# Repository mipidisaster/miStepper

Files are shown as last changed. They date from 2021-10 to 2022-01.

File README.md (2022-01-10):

# miStepper
This library contains the files and support for creating and installed code for the miStepper Device.e with this device).

# Linked libraries:
## milibrary
This library makes use of an extra repository - ['milibrary'](https://github.com/mipidisaster/miLibrary), which is not included within this repository; due to it being a seperate one. So this will need to be included...
> It doesn't matter were this is stored, however it should be at a high enough level that any lower level scripts can make reference to it.

```
<project root>
  ├─ milibrary
  │      └─ <contents>
  └─ < other folders >
```

# Stack overview
> To be added

# Build Tree
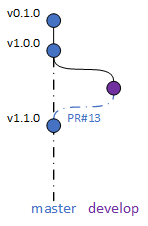
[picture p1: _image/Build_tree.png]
build tree


v1.1.0
* Changes made to the software to incorporate the motor HAL - Fan/Stepper, as well as changes to the USART interface (making it common with the 'miStepper_ROS' repository
* Issues [#4](https://github.com/mipidisaster/miStepper/issues/4) and [#5](https://github.com/mipidisaster/miStepper/issues/5) fixed
* Issue [#7](https://github.com/mipidisaster/miStepper/issues/7), partial progress has been made on working this - mainly that a single task now exists for the motors
* Submodules introduced for the 'miStepper_ROS' and 'miLibrary' repositories so as to manage which version(s) are appliable to this

v1.0.0
* Major update of build, changing the electronics (PCB):
  1. PCB/Electronics updated to include new Stepper IC - (issue [#1](https://github.com/mipidisaster/miStepper/issues/1))
  2. Hardware filtering on the voltage/current monitors
  3. Extra temperature sensors added - 2 onboard sensors, and 2 external sensors
  4. CAN interface improved, such that it not is compliant to the protocol/hardware
  5. 4 layer PCB, to aid thermal cooling

* Software code updated:
  1. Supports latest release of 'milibrary' - [v0.2.1](https://github.com/mipidisaster/miLibrary/tree/v0.2.1)
     * Closing issue [#3](https://github.com/mipidisaster/miStepper/issues/3)
  2. Update to support latest hardware additions
  > Note, external sensor support not provided currently, to be added in next release
  
  3. Re-structing of the code, such that it follows the ['Layered Software Architecure'](https://github.com/mipidisaster/miLibrary/wiki/Software-Architecture) as per milibrary wiki - (issue [#2](https://github.com/mipidisaster/miStepper/issues/2))

v0.1.0
* Initial release (to be used with [milibrary v0.1.0](https://github.com/mipidisaster/miLibrary/tree/v0.1.0))

# Wiki
The wiki for this can be found within the Github repository for this - > to be added

See https://github.com/mipidisaster/miLibrary/wiki for basic information on Eclipse setup/remote ROS downloading...

# Issues
If you find any issues with this library, please capture them within the Github repository issue area - https://github.com/mipidisaster/miStepper/issues.

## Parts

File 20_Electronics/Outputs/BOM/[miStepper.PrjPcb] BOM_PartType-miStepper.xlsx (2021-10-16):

Comment | Description | Designator | Footprint | LibRef | Value | Quantity | Layer
Res | Resistor | R10, R11, R12, R13 | RESC2012X06N (0805) | Res | 680mOhm/0.5W | 4 | Top
600R @ 100MHz | Inductor with ferrite bead | L1 | INDC1608X06N | Ferrite Bead | 600R @ 100MHz | 1 | Bottom
Cap Semi | Capacitor (Semiconductor SIM Model) | C14 | CAPC3216X06N (1206) | Cap Semi | 330nF/50V | 1 | Bottom
Cap Semi | Capacitor (Semiconductor SIM Model) | C12, C15, C18, C23_A, C23_C, C24_A, C24_C | CAPC1608X06N (0603) | Cap Semi | 100nF +/-5% | 7 | Bottom, Bottom, Top, Bottom, Bottom, Bottom, Bottom
Cap Semi | Capacitor (Semiconductor SIM Model) | C2, C3, C4, C5, C9, C20, C22, C25 | CAPC1608X06N (0603) | Cap Semi | 100nF | 8 | Top, Top, Bottom, Bottom, Bottom, Bottom, Top, Bottom
Res | Resistor | R14, R15 | RESC1608X06N (0603) | Res | 47k | 2 | Bottom
Res | Resistor | R8 | RESC1608X06N (0603) | Res | 39k | 1 | Bottom
Cap Pol | Polarized Capacitor (Surface Mount) | C13 | CAPAE7066X77M | Cap Pol | 33uF/50V | 1 | Top
Res | Resistor | R16 | RESC1608X06N (0603) | Res | 22k | 1 | Bottom
Res | Resistor | R9 | RESC1608X06N (0603) | Res | 18k | 1 | Top
Cap Semi | Capacitor (Semiconductor SIM Model) | C19, C21 | CAPC1608X06N (0603) | Cap Semi | 10uF | 2 | Bottom, Top
Cap Semi | Capacitor (Semiconductor SIM Model) | C7, C16 | CAPC1608X06N (0603) | Cap Semi | 10nF | 2 | Bottom
Res | Resistor | R1, R19, R20 | RESC1608X06N (0603) | Res | 10K | 3 | Top, Bottom, Bottom
Res | Resistor | R3, R5, R17, R21_A, R21_C | RESC1608X06N (0603) | Res | 9.76k +/-1% | 5 | Bottom, Bottom, Top, Bottom, Bottom
Res | Resistor | R2 | RESC1608X06N (0603) | Res | 7.5k | 1 | Top
Res | Resistor | R4 | RESC1608X06N (0603) | Res | 6.49k +/-1% | 1 | Bottom
Cap Semi | Capacitor (Semiconductor SIM Model) | C1 | CAPC1608X06N (0603) | Cap Semi | 4.7uF | 1 | Bottom
Res | Resistor | R18 | RESC1608X06N (0603) | Res | 4.32k +/-1% | 1 | Top
Res | Resistor | R6 | RESC1608X06N (0603) | Res | 1.96k +/-1% | 1 | Bottom
Cap Semi | Capacitor (Semiconductor SIM Model) | C6, C8 | CAPC1608X06N (0603) | Cap Semi | 1uF | 2 | Bottom
Cap Semi | Capacitor (Semiconductor SIM Model) | C11, C17 | CAPC1608X06N (0603) | Cap Semi | 1nF | 2 | Top
Res | Resistor | R7 | RESC1608X06N (0603) | Res | 1k | 1 | Bottom
Cap Semi | Capacitor (Semiconductor SIM Model) | C10 | CAPC1608X06N (0603) | Cap Semi | 0.1uF | 1 | Bottom
Res | Resistor | RS1_A, RS1_C | RESC2012X06N (0805) | Res | 0.05+/-1% | 2 | Bottom
AD7415ARTZ-1500RL7 | I2C Temperature Sensor | U4, U7 | SOT95P280X145-5N | AD7415ARTZ-1500RL7 |  | 2 | Bottom, Top
AS5047D |  | U9 | TSSOP14 | AS5047D |  | 1 | Bottom
CS30xL | High side current sense high voltage op amp | U8_A, U8_C | SOT95P280X145-5N | CS30xL |  | 2 | Bottom
GY-BME280 BREAKOUT |  | U5, U6 | GY-BME280 BREAKOUT | GY-BME280 BREAKOUT |  | 2 | None
JST PH Series, 2mm Pitch 6 Way 1 Row Right Angle PCB Header, Solder Termination, 2A Source: Datasheet | Custom header for miStepper | JP2 | S6B-PH-SM4-TB(LF)(SN) | miStepper-Connector |  | 1 | None
MC33873 | Motor | JP4 | JP1Y | MC33873 |  | 1 | Top
NEMA17 | Stepper Motor | JP3 | S4B-PH-SM4-TB(LF)(SN) | NEMA17 |  | 1 | Top
NMOS-2 | N-Channel Power MOSFET | Q1 | SOT230P700X180-4N | NMOS-2 |  | 1 | Top
Option_Res | Resistor | SB1 | RESC1608X06N (0603) | Option_Resistor |  | 1 | Top
Schottky Diode | Schottky Rectifier | D1 | SODFL350X115-2N | Diode |  | 1 | Bottom
SN65HVD233 | 3.3V CAN Bus Transceiver | U2 | SOIC127P600X175-8N | SN65HVD23x |  | 1 | Top
ST-LINK_USART | Header, 8-Pin | JP1 | MHDR1X8 | MHDR1X8 |  | 1 | Top
STM32L431CC | STM32 ARM-based 32-bit MCU with 32 Kbytes Flash, 48-pin LQFP, Industrial Temperature | U1 | LQFP48_L | STM32L431CC |  | 1 | Top
STSPIN820 | Stepper IC | U3 | QFN50P400X400X110-25N | STSPIN820 |  | 1 | Top

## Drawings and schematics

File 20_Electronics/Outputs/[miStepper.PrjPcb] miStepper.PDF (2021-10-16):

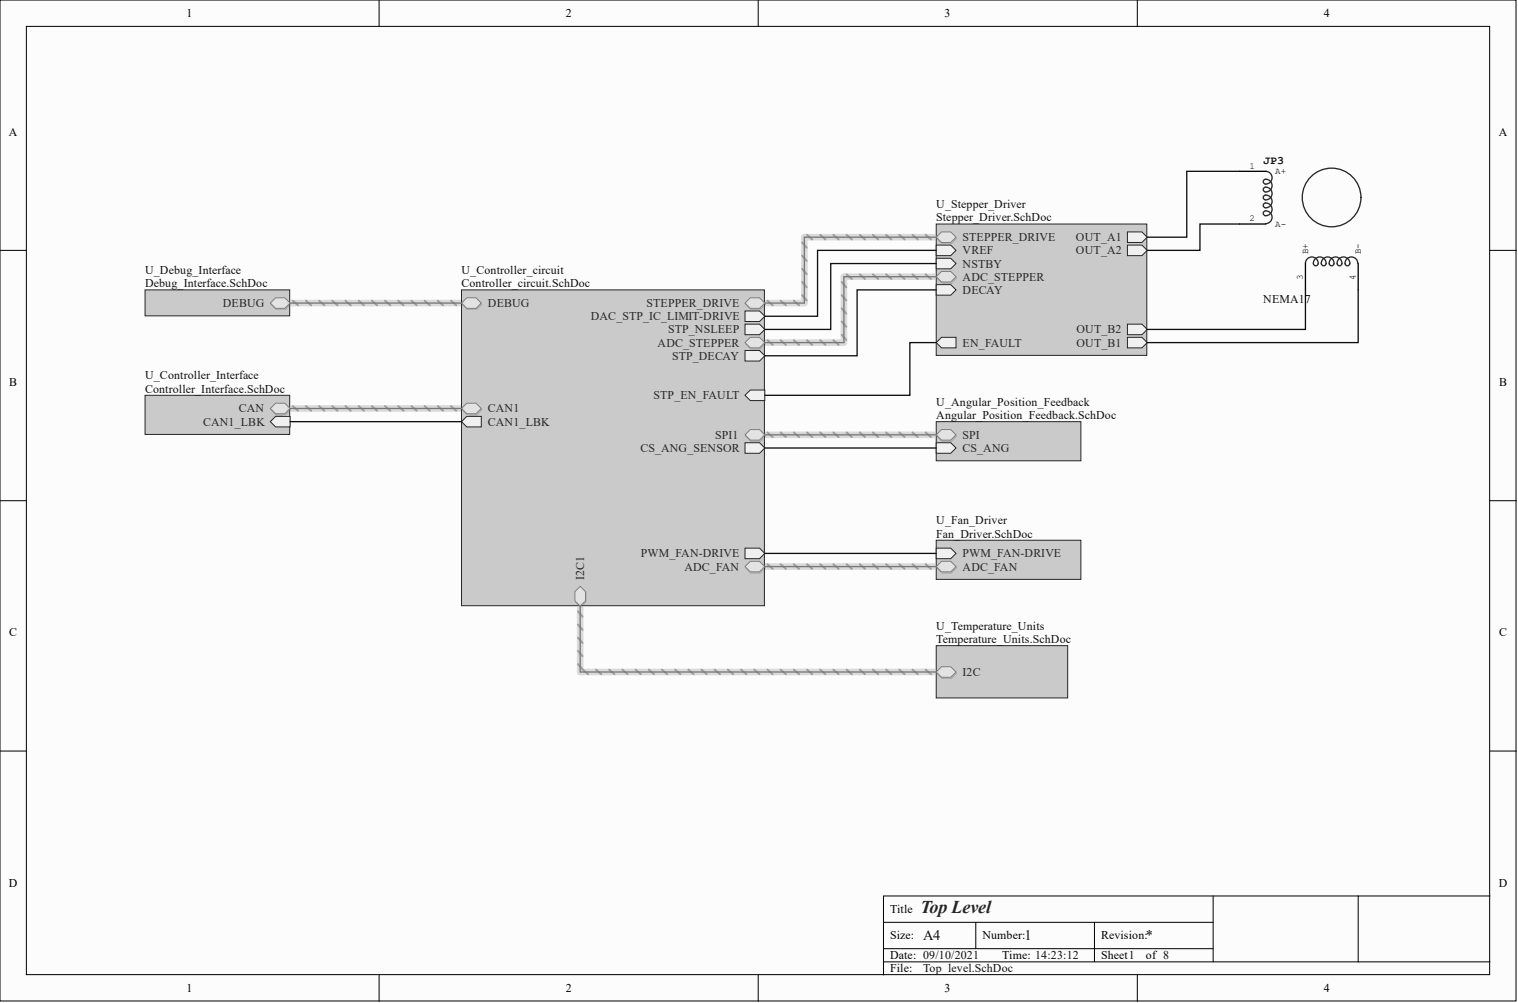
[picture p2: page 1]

Title Top Level

Size: A4 | Number: 1 | Revision: *
Date: 09/10/2021 Time: 14:23:12 | | Sheet of

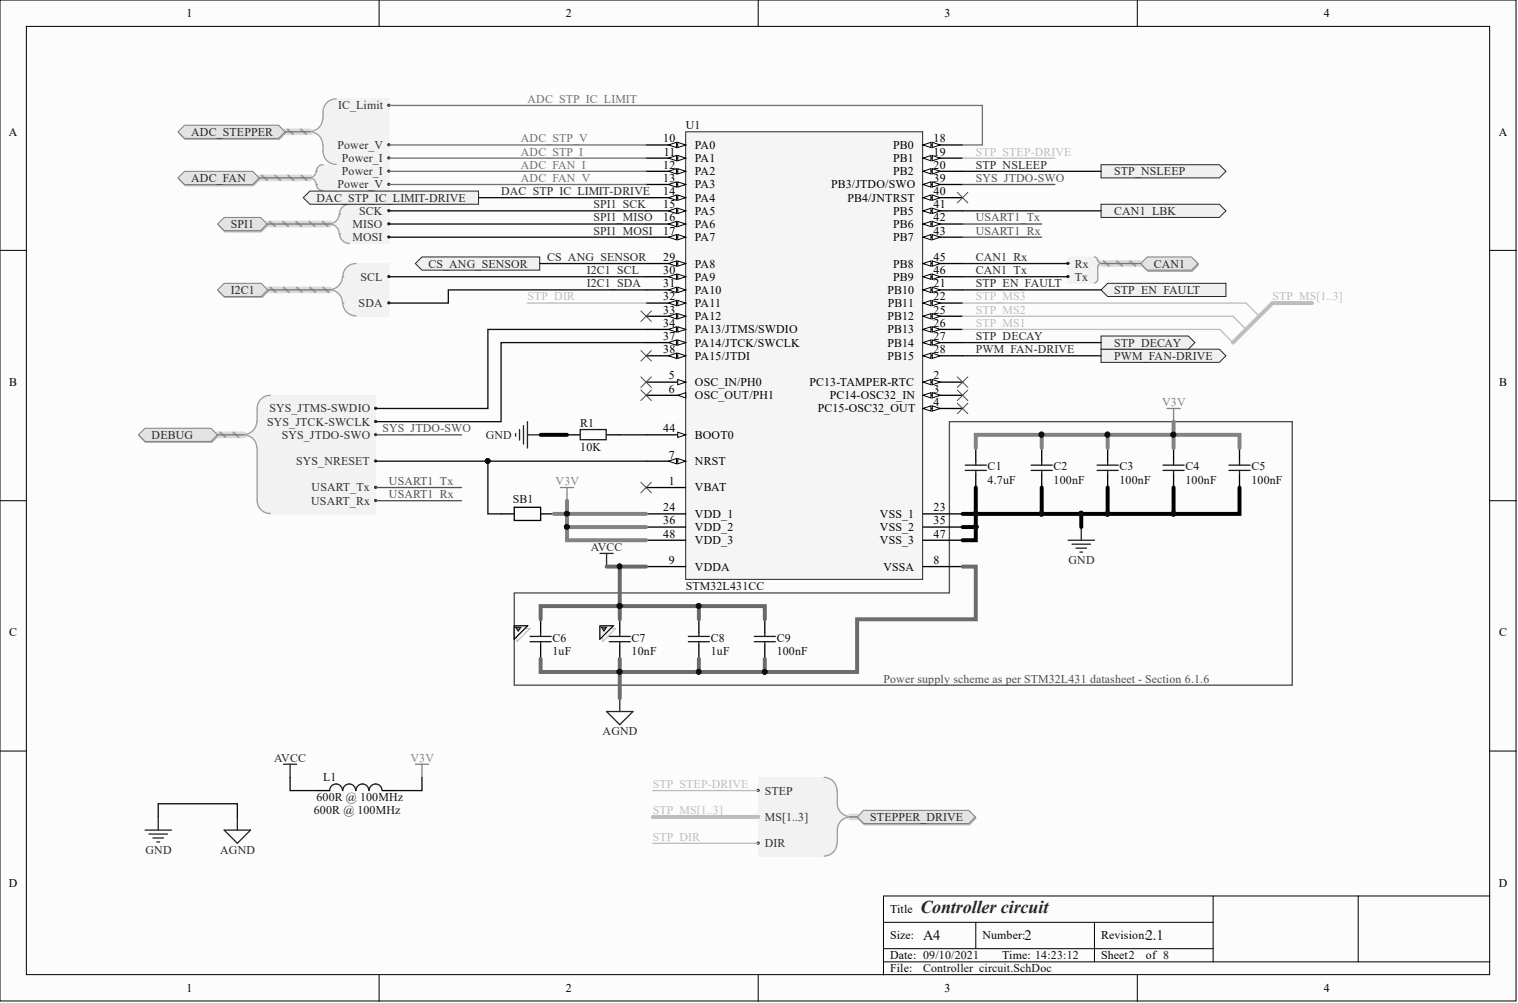
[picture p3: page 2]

Power supply scheme as per STM32L431 datasheet - Section 6.1.6

Title Controller circuit

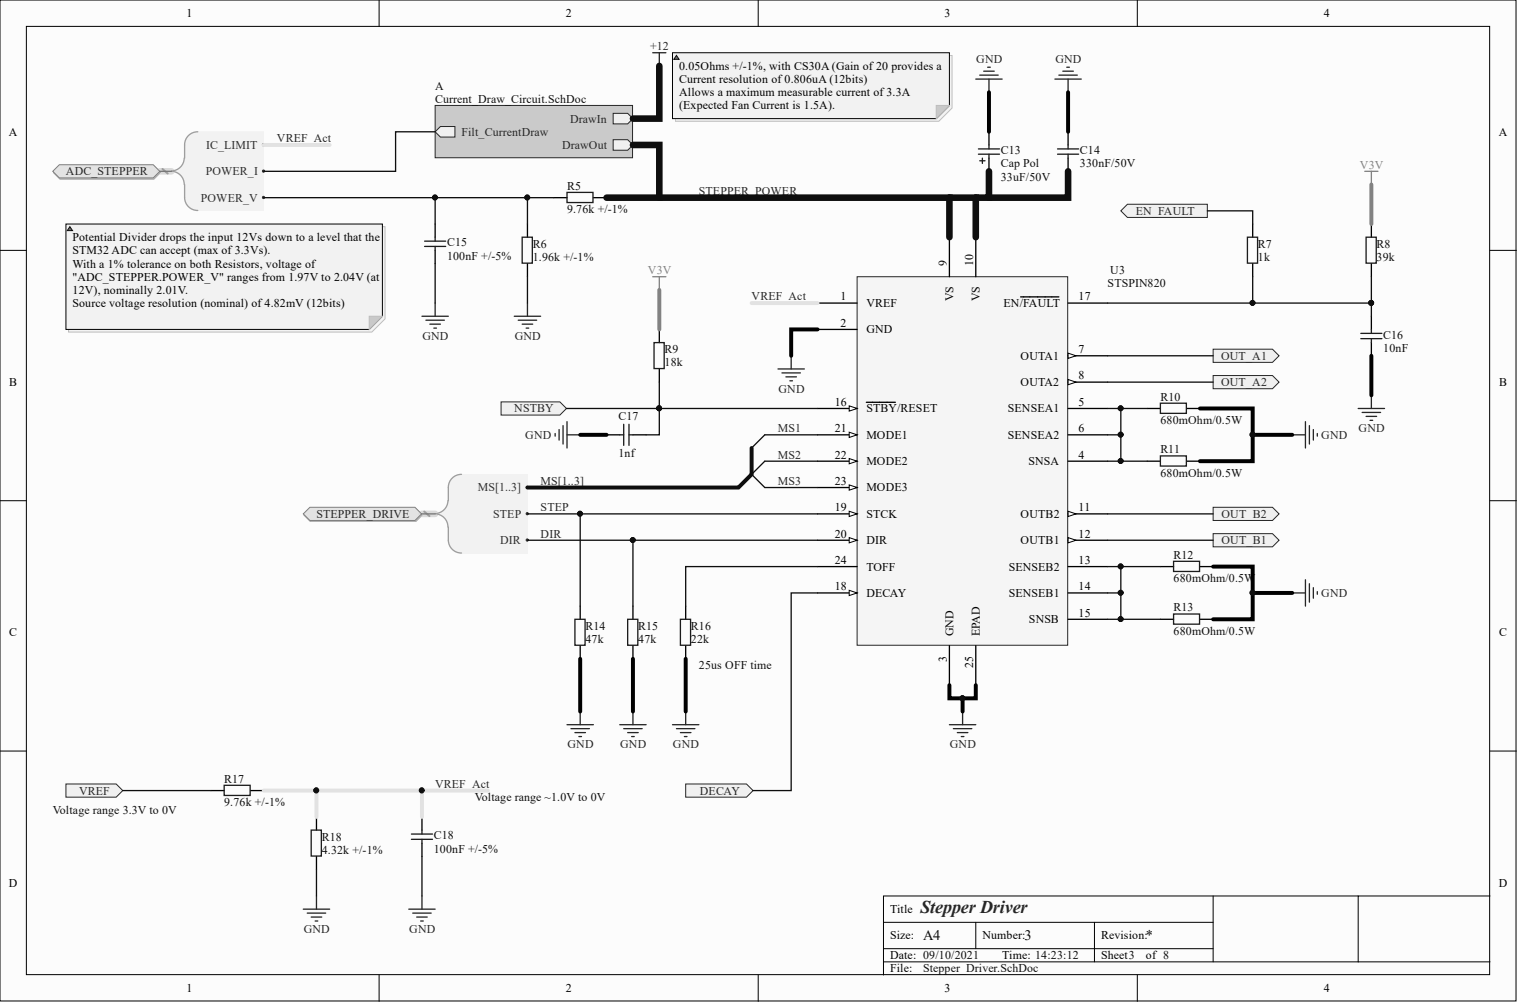
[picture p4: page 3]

0.05Ohms +/-1%, with CS30A (Gain of 20 provides a
Current resolution of 0.806uA (12bits)
Allows a maximum measurable current of 3.3A
(Expected Fan Current is 1.5A).

Potential Divider drops the input 12Vs down to a level that the
STM32 ADC can accept (max of 3.3Vs).
With a 1% tolerance on both Resistors, voltage of
"ADC_STEPPER.POWER_V" ranges from 1.97V to 2.04V (at
12V), nominally 2.01V.
Source voltage resolution (nominal) of 4.82mV (12bits)

GND 2

MODE1 21 MODE2 22 MODE3 23 STCK 19 | 680mOhm/0.5W R11

TOFF 24
DECAY 18 | 680mOhm/0.5W

Title Stepper Driver

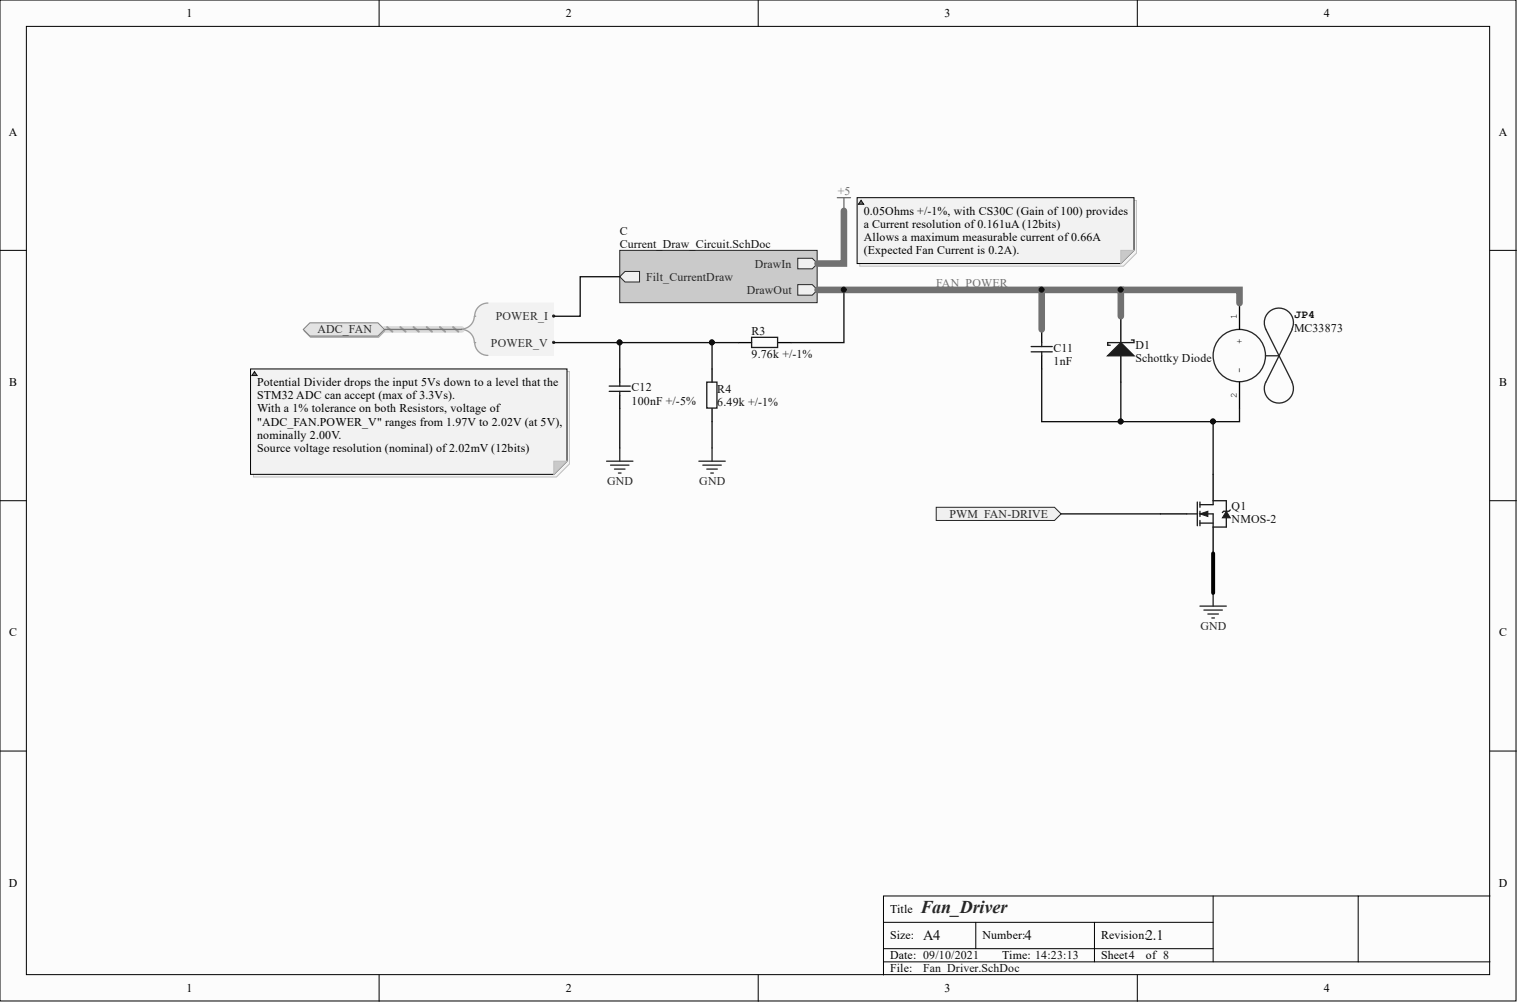
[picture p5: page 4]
DrawIn DrawOut; ial D; o a level t; hat t; t (max of 3.3; lerance o; h Res; ors, v; tage of; V" ran; ges from 1.9; urce v; tage res; nal) of 2.0; hms +/-1; 0C (Gai; 0) pro; a Curren; t res; s a max; imum meas; le curren; pected Fan Curren

der dro
DC can accep

T i t l e Fan_ Driver

Size: A | N umber: | Rev i s n 2.1

/ T ime: : | | Sheet f

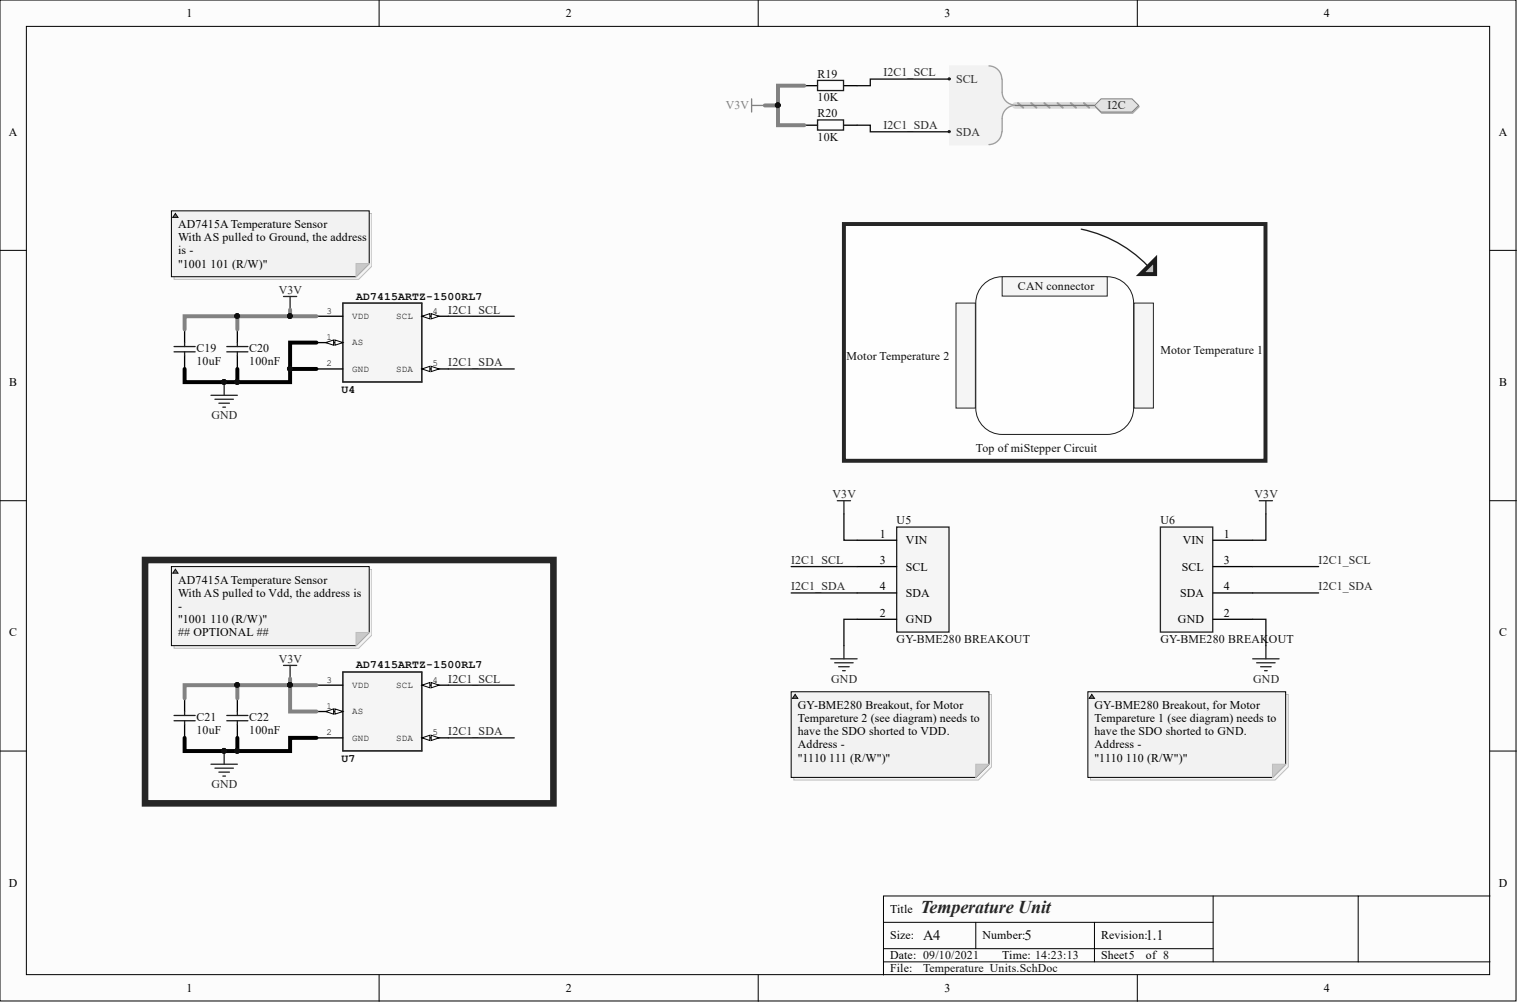
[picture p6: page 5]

AD7415A Temperature Sensor
With AS pulled to Ground, the address

Top of miStepper Circuit

With AS pulled to Vdd, the address is
## OPTIONAL ##

GY-BME280 Breakout, for Motor
Tempareture 2 (see diagram) needs to
have the SDO shorted to VDD.
Address -

Tempareture 1 (see diagram) needs to
have the SDO shorted to GND.

Title Temperature Unit

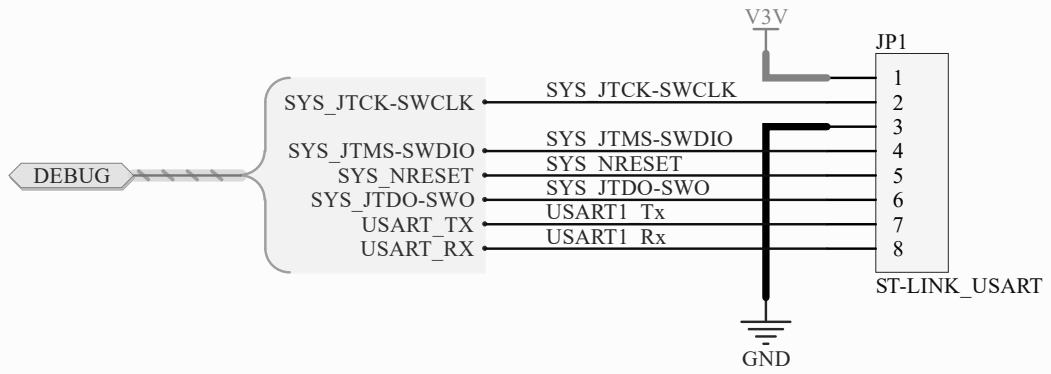
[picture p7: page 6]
Debug Interface6; PIJP102 NLSYS0JTCK0SWCLK; PODEBUG; PIJP106 NLSYS0JTDO0SWO; PIJP104 NLSYS0JTMS0SWDIO PIJP105 NLSYS0NRESET; PIJP108 NLUSART10Rx; PIJP107 NLUSART10Tx; PODEBUG0SYS0JTCK0SWCLK PODEBUG0SYS0JTDO0SWO PODEBUG0SYS0JTMS0SWDIO PODEBUG0SYS0NRESET PODEBUG0USART0RX PODEBUG0USART0TX

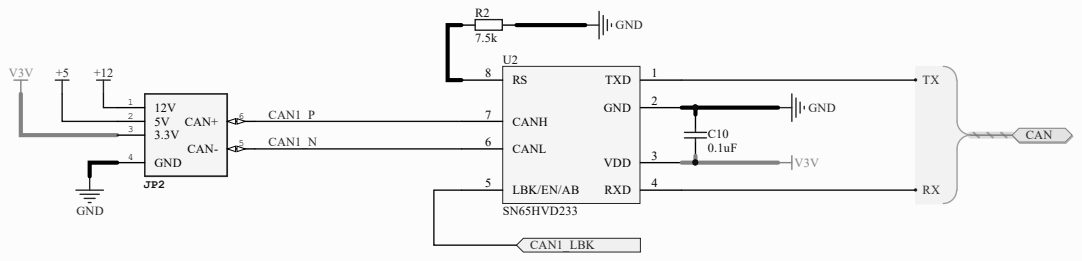
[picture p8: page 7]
RXD; 4 LBK/EN/AB 5; CANL 6; CANH 7; GND 4

Title Board Interfaces

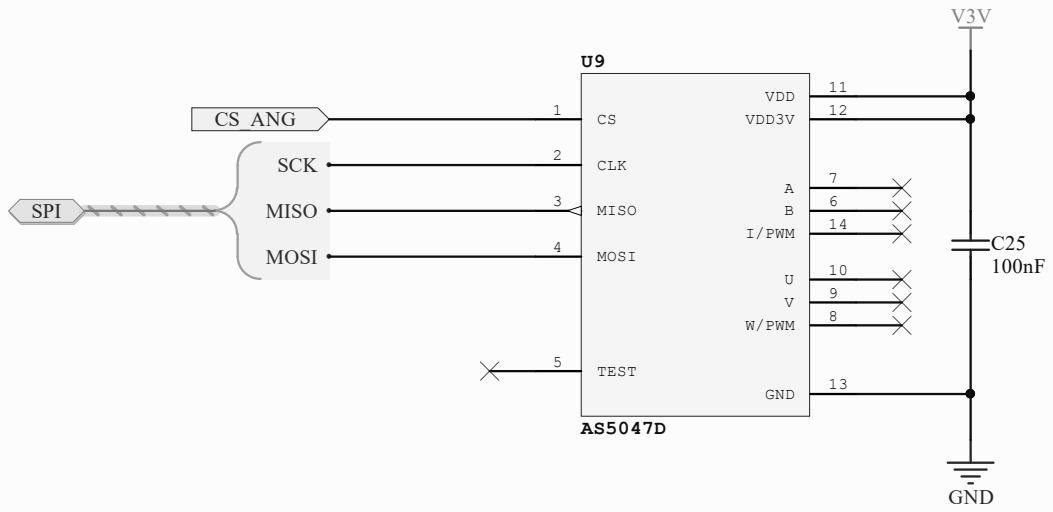
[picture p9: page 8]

T i t l e Angular Position Feedb ack

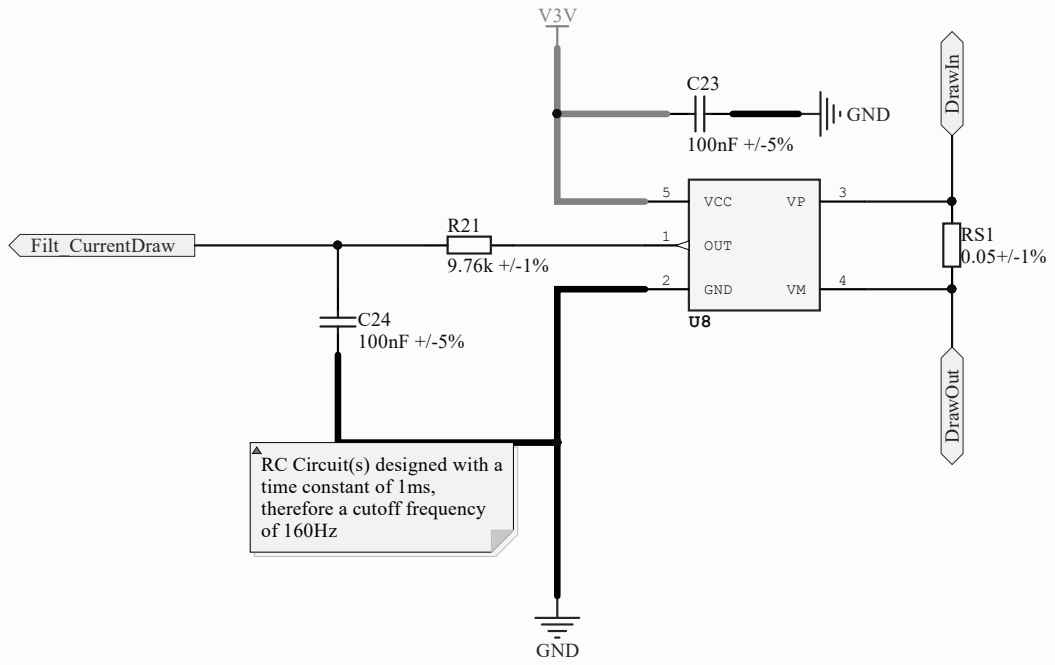
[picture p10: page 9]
DrawIn DrawOut; RC Circu; t(s) des; ned w; ime co; t of 1ms, herefore a cu; off freq

T i t l e Current Draw Senso r

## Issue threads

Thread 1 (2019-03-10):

Change Stepper IC

mipidisaster, 2019-03-10:
See about updating the Stepper IC to an STMicroelectronics component: STSPIN820
As gives better stepping control - 1/256 of a step!!

mipidisaster, 2019-03-10:
Check the schematic and gerbers of the dev board - IHM14A1

mipidisaster, 2021-10-16:
At v1.0.0 (585d8fb) STSPIN820 has been added to the PCB

Closed 2021-10-16.

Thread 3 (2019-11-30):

Highest Microstep not selected

mipidisaster, 2019-11-30:
During test phase - StepperTest2 - it was noticed that the highest microstep resolution (1/16) couldn't be selected with the current software version.
Testing has continued, however issue needs to be resolved.

mipidisaster, 2019-11-30:
Expect that the issue could be due to the Stepper driver, #2 (Library project).
Additionally the calcPosition logic needs to be looked into in more detail...

mipidisaster, 2019-12-01:
Found the issue:
https://github.com/mipidisaster/miStepper/blob/09903c70077cd2d019771f57bcddb5c358ebf495/30_Software/Embed/tasks/outputs/stepper_hal/stepper_hal.h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

Maximum gear should be 0x07!

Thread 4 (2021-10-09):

Stepper HAL missing

mipidisaster, 2021-10-09:
With the latest build there are no HAL interfaces for the Stepper task. So unable to actually control the motor in any way.

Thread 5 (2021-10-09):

USART controller missing links to the FAN/STEPPER

mipidisaster, 2021-10-09:
Current USART task - built off devel - "miStepperUSART" is missing connections for the FAN and STEPPER controller

mipidisaster, 2022-01-10:
Issue closed with pull request #13

Closed 2022-01-10.

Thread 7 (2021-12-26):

Driver tasks

mipidisaster, 2021-12-26:
Might be worth removing the specific tasks for the stepper motor and fan motor control. As this could be simply a function which updates the parameters for the drivers, removing the need for seperate tasks which basically do nothing...

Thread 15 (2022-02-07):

BME280 introduction to miStepper device

mipidisaster, 2022-02-07:
With the new hardware standard for miStepper, there are 2 external temperature sensors to be used to get the temperature of the motor.
These sensors are BME280 connected via I2C. This needs to be added to the build

mipidisaster, 2022-03-05:
This is a MINOR version introduction - so version number should go up by 0.1.0 minimum.

mipidisaster, 2022-03-06:
This is a MINOR version introduction - so version number should go up by 0.1.0 minimum (miStepper).

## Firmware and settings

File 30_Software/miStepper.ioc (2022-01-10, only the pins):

Mcu.UserName=STM32L431CBTx
PA0.GPIO_Label=ADC_STP_V
PA0.Signal=ADCx_IN5
PA1.GPIO_Label=ADC_STP_I
PA1.Signal=ADCx_IN6
PA10.Signal=I2C1_SDA
PA11.GPIO_Label=STP_DIR
PA11.Signal=GPIO_Output
PA2.GPIO_Label=ADC_FAN_I
PA2.Signal=ADCx_IN7
PA3.GPIO_Label=ADC_FAN_V
PA3.Signal=ADCx_IN8
PA4.GPIO_Label=DAC_STP_IC_LIMIT-DRIVE
PA4.Signal=COMP_DAC11_group
PA5.Signal=SPI1_SCK
PA6.Signal=SPI1_MISO
PA7.Signal=SPI1_MOSI
PA8.GPIO_Label=CS_ANG_SENSOR
PA8.Signal=GPIO_Output
PA9.Signal=I2C1_SCL
PB0.GPIO_Label=ADC_STP_IC_LIMIT
PB0.Signal=ADCx_IN15
PB1.GPIO_Label=STP_STEP-DRIVE
PB1.Signal=TIM1_CH3N
PB11.GPIO_Label=STP_MS3
PB11.Signal=GPIO_Output
PB12.GPIO_Label=STP_MS2
PB12.Signal=GPIO_Output
PB13.GPIO_Label=STP_MS1
PB13.Signal=GPIO_Output
PB14.GPIO_Label=STP_DECAY
PB14.Signal=GPIO_Output
PB15.GPIO_Label=PWM_FAN-DRIVE
PB15.Signal=S_TIM15_CH2
PB2.GPIO_Label=STP_NSLEEP
PB2.Signal=GPIO_Output
PB6.Signal=USART1_TX
PB7.Signal=USART1_RX

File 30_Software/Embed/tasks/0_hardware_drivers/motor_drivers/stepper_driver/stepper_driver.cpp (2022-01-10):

/**************************************************************************************************
 * @file        stepper_driver.cpp
 * @author      Thomas
 * @brief       Source file for Stepper Motor task handler
 **************************************************************************************************
  @ attention

  << To be Introduced >>

 *************************************************************************************************/
#include "tasks/0_hardware_drivers/motor_drivers/stepper_driver/stepper_driver.hpp"
#include "tasks/0_hardware_drivers/motor_drivers/motor_driver.h"
// C System Header(s)
// ------------------
#include <stdint.h>

// C++ System Header(s)
// --------------------
// None

// Other Libraries
// ---------------
// None

// Project Libraries
// -----------------
#include "stm32l4xx_hal.h"              // Include the HAL library
#include "main.h"                       // Include main header file, as this contains the defines
                                        // for GPIO signals
#include "tim.h"                        // Include the timer header file, as this contains the
                                        // htim1 handle

#include "tasks/0_hardware_drivers/motor_drivers/stepper_driver/stepper_driver_parameters.hpp"

#include "tasks/1_hardware_arbitration_layer/istepper_hal.hpp"
#include "tasks/1_hardware_arbitration_layer/itimer_hal.hpp"

#include "FileIndex.h"
//~~~~~~~~~~~~~~~~~~~~
#include FilInd_GPIO___HD               // Include the GPIO class handler
#include FilInd_StpCOREHD               // Include the Stepper CORE class handler

#ifdef zz__StepperDMAControl__zz
#include FilInd_StpDMA_HD               // Include the Stepper DMA class handler

#else
#include FilInd_StpTIM_HD               // Include the Stepper TIM class handler

#endif
//=================================================================================================

extern DMA_HandleTypeDef hdma_tim1_ch3; // Declare a DMA handle used for the TIM1

namespace _motor::_stepper {
/**************************************************************************************************
 * Define any private variables
 * ~~~~~~~~~~~~~~~~~~~~~~~~~~~~
 *************************************************************************************************/
#ifdef zz__StepperDMAControl__zz
static StepperDMA   *lc_handle;         // Pointer to the StepperDMA class handle, for interrupt
                                        // use

#else
static StepperTIM   *lc_handle;         // Pointer to the StepperTIM class handle, for interrupt
                                        // use

#endif

/**************************************************************************************************
 * Define any private function prototypes
 * ~~~~~~~~~~~~~~~~~~~~~~~~~~~~~~~~~~~~~~
 *************************************************************************************************/
uint32_t determineCountRate(uint8_t microstep);

//=================================================================================================

/**
  * @brief:  Setup and initialise the Stepper Class
  * @param:  void const, not used
  * @retval: None (void output)
  */
void setup(void) {
    // Generate the GPIO pins outside of 'Stepper' handle scope
    // ========================================================
    static GPIO    STP_DIR(    STP_DIR_GPIO_Port,       STP_DIR_Pin,        GPIO::kOutput);
    static GPIO    STP_MS[3]={{STP_MS1_GPIO_Port,       STP_MS1_Pin,        GPIO::kOutput},
                              {STP_MS2_GPIO_Port,       STP_MS2_Pin,        GPIO::kOutput},
                              {STP_MS3_GPIO_Port,       STP_MS3_Pin,        GPIO::kOutput} };

    static GPIO    STP_DECAY(  STP_DECAY_GPIO_Port,     STP_DECAY_Pin,      GPIO::kOutput);
    static GPIO    STP_SLEEP(  STP_NSLEEP_GPIO_Port,    STP_NSLEEP_Pin,     GPIO::kOutput);


    // Disable the Stepper IC, by pulling ENABLE/SLEEP high, and RESET low:
    STP_SLEEP.setValue(GPIO::State::kLow);      // Set Sleep  pin to LOW  '0'   (Device Asleep)
    STP_DECAY.setValue(GPIO::State::kLow);      // Set Decay  pin to Low  '0'   (Mixed Decay mode)
    // Create Stepper(DMA) class
    // =========================
#ifdef zz__StepperDMAControl__zz
    static StepperDMA
#else
    static StepperTIM
#endif
            STSPIN820(&htim1, &hdma_tim1_ch3,
                // Generate the output signal for STEP 'pulse'
            ( TIM_CCxN_ENABLE << TIM_CHANNEL_3 ),   // The output channel pin for enabling the
                                                    // output for 'Capture/Compare 3'
            // Linked GPIO pins - Reset(Sleep), Direction and Microstep
            &STP_SLEEP, &STP_DIR, &STP_MS[0], 3,
            200 * 256,

   /* Setup the 'Stepper' handler so that
    *      [1] The linked DMA used to generate the STEP 'pulse', which is Capture/Compare 3
    *      [2] Provide the BIT position for enabling/disabling in 'DIER' register for TIM linkage
    *          to DMA
    *      [3] Provide the BIT position within TIM 'EGR' to generate a 'Capture/Compare 3' event
    *      [4] Provide the BIT position within TIM 'SR' to check for a 'Capture/Compare 3' event
    *********************************************************************************************/
            StepperCore::HrdSetup {.PulseDMAAddress  = (uint32_t) &htim1.Instance->CCR3,    //[1]
                                   .EnbTIMDMA        = TIM_DMA_CC3,                         //[2]
                                   .PulsEGRBit       = TIM_EVENTSOURCE_CC3,                 //[3]
                                   .PulsSRBit        = TIM_FLAG_CC3                         //[4]
                                  }
            );

    lc_handle = &STSPIN820;         // Link STSPIN820 class to global pointer (for ISR)

}

/**
  * @brief:  Tasks to do only ONCE in the loop
  * @param:  void const, not used
  * @retval: None (void output)
  */
void firstpass(void) {
   // Nothing required currently for initial pass.
}
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

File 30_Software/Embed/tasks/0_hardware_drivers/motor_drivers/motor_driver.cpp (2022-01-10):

/**************************************************************************************************
 * @file        motor_driver.cpp
 * @author      Thomas
 * @brief       Source file for Motor task handler
 **************************************************************************************************
  @ attention

  << To be Introduced >>

 *************************************************************************************************/
#include "tasks/0_hardware_drivers/motor_drivers/motor_driver.h"
// C System Header(s)
// ------------------
#include <stdint.h>
#include "cmsis_os.h"                   // Header for introducing FreeRTOS to device

// C++ System Header(s)
// --------------------
// None

// Other Libraries
// ---------------
// None

// Project Libraries
// -----------------
#include "main.h"                       // Include main header file, as this contains the defines

#include "tasks/0_hardware_drivers/motor_drivers/motor_driver_parameters.hpp"

#include "tasks/0_hardware_drivers/motor_drivers/fan_driver/fan_driver.hpp"
#include "tasks/0_hardware_drivers/motor_drivers/stepper_driver/stepper_driver.hpp"

#include "tasks/1_hardware_arbitration_layer/ihal_management.hpp"

#include "tasks/1_hardware_arbitration_layer/ifan_hal.hpp"
#include "tasks/1_hardware_arbitration_layer/istepper_hal.hpp"
#include "tasks/1_hardware_arbitration_layer/itimer_hal.hpp"

//=================================================================================================
/**************************************************************************************************
 * Define any private variables
 * ~~~~~~~~~~~~~~~~~~~~~~~~~~~~
 *************************************************************************************************/
// None

/**************************************************************************************************
 * Define any private function prototypes
 * ~~~~~~~~~~~~~~~~~~~~~~~~~~~~~~~~~~~~~~
 *************************************************************************************************/
// None

//=================================================================================================

/**
  * @brief:  Motor Hardware Abstraction Layer task (covering both Fan and Stepper configuration
  *          and monitoring)
  * @param:  void const, not used
  * @retval: None (void output)
  */
void vMotorHAL(void const * argument) {
/*---------------------------[  Setup HAL based classes for H/W   ]---------------------------*/
    _motor::_fan::setup();
    _motor::_stepper::setup();

/*---------------------------[    Device Fault flag generation    ]---------------------------*/
    // Interface signal initialisation & interrupt setup
    // =================================================
    _ihal::_ifan::interfaceInitialise();
    _ihal::_istepper::interfaceInitialise();

    uint8_t enable      = _ihal::_istepper::enable.content;
    uint8_t microstep   = _ihal::_istepper::microstep.content;
    uint8_t direction   = _ihal::_istepper::direction.content;
    uint16_t frequency  = _ihal::_istepper::frequency.content;

/*---------------------------[        FAN Device Main Loop        ]---------------------------*/
    /****************************************************************************/
    /****************************************************************************/
    uint8_t first_pass = 1;     // Indicate that this is the first time going through this task

    uint16_t previous_recorded_time = _ihal::_itimer::tic();
    uint32_t previous_wake_time = osKernelSysTick();    // Capture start time of task within Kernel
                                                        // time
    /* Infinite loop */
    for(;;) {
        uint16_t cal_task_period = _ihal::_itimer::toc(&previous_recorded_time);

        // Capture any new updates to input signals and link to local internals
        if (first_pass == 1) {                  // On first pass of this task, it owns its input
                                                // as well
            _motor::_fan::firstpass();
            _motor::_stepper::firstpass();
        }
        float current_demand = _ihal::getValue(&_ihal::_ifan::demand);
        _motor::_fan::updatespeed(current_demand);

        if ((enable     != _ihal::_istepper::enable.content) ||
            (microstep  != _ihal::_istepper::microstep.content) ||
            (direction  != _ihal::_istepper::direction.content) ||
            (frequency  != _ihal::_istepper::frequency.content))
        {
            _motor::_stepper::updatespeed(_ihal::_istepper::enable.content,
                                          _ihal::_istepper::microstep.content,
                                          _ihal::_istepper::direction.content,
                                          _ihal::_istepper::frequency.content);
        }

        enable      = _ihal::_istepper::enable.content;
        microstep   = _ihal::_istepper::microstep.content;
        direction   = _ihal::_istepper::direction.content;
        frequency  = _ihal::_istepper::frequency.content;
        _motor::_stepper::calposition();

        first_pass = 0;             // Update this flag such that it now indicates that first
                                    // pass has completed
        /****************************************************************************/
        /****************************************************************************/
        /* End of task, will now wait defined period--------------------------------*/
        _ihal::_itimer::recordTimeSheet(  _ihal::TimedTasks::kFAN, cal_task_period,
                                          _ihal::_itimer::toc(previous_recorded_time)  );

        osDelayUntil(&previous_wake_time, _motor::_param::ktask_rate);
        // Put the task in "DELAYED" state for the defined period
    }
}

///////////////////////////////////////////////////////////////////////////////////////////////////
/**************************************************************************************************
 * ===============================================================================================
 * Local functions
 * ===============================================================================================
 *************************************************************************************************/
///////////////////////////////////////////////////////////////////////////////////////////////////
// None

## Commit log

2019-03-09 Initial version of 'miStepper' project, software is working correctly
    [miStepper.ioc]
2019-03-10 Electronics of version 1 of 'miStepper' hardware
    [ComponentCals.xlsx, StepperController_v1-0.brd, StepperController_v1-0.sch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]
2019-06-25 Embedded functions updated to provide a set of data via USART to a computer - Raspberry Pi, and read back a set of commands. This is going to be used to design the internal logic of the miStepper
2019-09-04 Configuration file for miStepper updated to include some information on how the Stepper motor task iteration rate should be determined + spreadsheets added
    [PacketTransmission.xlsx, Timings.xlsx]
2019-09-15 SPI/I2C tasks updated to align with updated design of SPIPeriph/I2CPeriph - such that it now uses just the arrays to link to the peripherals
2019-09-15 ADC task updated to include averaging of the 'ADC1_ConvPSeq'values captured per ADC run
2019-09-18 Update to the USART task due to update to the UARTPeriph class, to utilise the 'Form system'; next update will be using the DMA instead of interrupt based communication
2019-09-28 All tasks updated such that they no longer receive in a parameter with the linked hardware. It is instead called within the cpp as an extern variable Additionally, UART updated to utilise DMA.
    warning has been added to ADC, on the DMA as current call doesn't allow for re-allocating DMA pointers (as STM32CubeMX thinks the HAL is locked)
2019-11-15 All tasks updated such that they no longer receive in a parameter pointing to variables/builds/etc. Additionally USART task updated to include DMA and CRC
2021-10-09 Update to 'miStepper.ioc' and version of 'STM32CubeMX' (v6.2.1) generates different outputs. Embed folder and contents updated to align with new stucture, as per miLibrary wiki (Software Architecture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
2021-10-09 Archieve within '20_Electronics' deleted as not required due to github
    [ComponentCals.xlsx, StepperController_v1-0.brd, StepperController_v1-0.sch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]
2021-10-09 Removing unrequired files within 'Embed' due to code update
    [PacketTransmission.xlsx]
2021-10-09 Task utilisation spreadsheet added, and updated Timings spreadsheet commited
    [Task_Utilisation.xlsx, Timings.xlsx]
2021-10-09 Task Utilisation updated based upon the latest code
    [Task_Utilisation.xlsx]
2021-10-16 Electronics schematics/GERBER files added for the mk2 version of the hardware. README file/Build Tree updated to state latest changes in next release
    [Angular_Position_Feedback.SchDoc, ComponentCals.xlsx, Controller_Interface.SchDoc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]
2021-12-23 USART driver updated to align with latest working version of the miStepperUART class from milibrary
2021-12-23 USART driver task updated to align with name changes to 'miStepperUSART' members
2021-12-23 USART interface file updated to include the 'Control' function which facilitates the commands from user - via miStepper_ROS - into the miStepper Device. Note that this currently only supports FAN con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
2022-01-10 Fan demand parameter updated, due to some of the name already being captured as part of the namespace. i.e. name space is '_ifan', so there is no need to call the parameter 'fan_demand'
2022-01-10 Ref issue #4 and #5. Introduced HAL interface for the actual Stepper motor, making use of the updates to milibrary 'miStepperUSART'.
    [fan_driver.cpp, istepper_hal.cpp, motor_driver.cpp]
2022-01-10 Current limit updates to support change is test motor
2022-01-10 Ref issue #7. Update to the STM32CubeMX file to support change in the tasks for the motors to a single task. Task_Utilisation spreadsheet updates to get memory levels for latest build
    [Task_Utilisation.xlsx]
